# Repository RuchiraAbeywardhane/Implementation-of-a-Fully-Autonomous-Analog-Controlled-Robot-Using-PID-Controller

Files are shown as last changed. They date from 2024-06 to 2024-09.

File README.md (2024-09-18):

# Analog Wall Following Robot
This is a group project done under the module EN2091 - Laboratory Practice and Projects, Semester 3, Department of Electronic and Telecommunication Engineering, University of Moratuwa. 

## Introduction

*  Wall following robot is a robot that follows a wall and travels keeping a constant distance from the wall. 
*  Wall following is a common task in many robotics competitions.
*  But the interesting point is our project was to build a robot that travels on the centerline between two walls using only analog electronics.
*  That means we couldn’t use microcontrollers according to the [guidelines](https://github.com/LasithaAmarasinghe/Analog-Wall-Follow-Robot/blob/main/Project_Guidelines.pdf).

IMG-20231206-WA0097

## Working Concept

*  Two sharp IR sensors measure the distance from the robot to the side walls.
*  The difference between the sharp IR sensor values is taken as the error signal and fed into a PID control circuit.
*  The PID output signal is fed to the adder and subtractor circuits.
*  The PID output and a comparator circuit generate two PWM signals with varying duty cycles.
*  Then using the motor driver, PWM signals are fed to the left and right wheels.
*  The robot tracks the walls and travels on the centerline between walls.
*  Additionally we added another sharp IR sensor to the front of the robot to control the speed of the robot.
*  The measured distance is compared with a predefined distance and the difference is taken as the error signal.
*  The error signal is fed to a PID control circuit.
*  A PWM signal is generated using the PID output and a comparator circuit.
*  This PWM signal acts as the Base speed of the robot.
*  Consequently the additional sharp IR sensor will vary the car's speed accordingly.
*  Therefore the car will accelerate and deaccelerate according to the distance of the wall infront it.



## Sub Circuits and Tasks

* [Instrumentation Amplifier](https://github.com/LasithaAmarasinghe/Analog-Wall-Follow-Robot/blob/main/Circuits/Instrumentation%20Amplifier.jpg)- Reduce noise in Sharp IR sensor outputs and amplify signals
* [PID circuit](https://github.com/LasithaAmarasinghe/Analog-Wall-Follow-Robot/blob/main/Circuits/PID.jpg)- Control the error signal smoothly using feedback
* [Adder & Subtractor](https://github.com/LasithaAmarasinghe/Analog-Wall-Follow-Robot/blob/main/Circuits/Adder%20%26%20Substractor.jpg)- Generate two PWM signals with varying duty cycles according to PID output
	* Motor 1= base speed + PID output
	* Motor 2= base speed - PID output
* [PWM circuit](https://github.com/LasithaAmarasinghe/Analog-Wall-Follow-Robot/blob/main/Circuits/PWM.jpg)- Generate two different comparator voltages for the two motors
	* Motor 1 duty cycle ∝ base speed + PID output
	* Motor 2 duty cycle ∝ base speed - PID output
* [Voltage Regulator](https://github.com/LasithaAmarasinghe/Analog-Wall-Follow-Robot/blob/main/Circuits/Voltage%20Regulator.png)- To get 3.3V and 5V for required parts accordingly
* [Speed Selector](https://github.com/LasithaAmarasinghe/Analog-Wall-Follow-Robot/blob/main/Circuits/Speed%20Selector.png)- Manually control the base speed

## Hardware Specifications

* [TL084CN ICs](https://github.com/LasithaAmarasinghe/Analog-Wall-Follow-Robot/blob/main/data%20sheets/TL084CN_GeneralPurposeAmplifier.pdf)
* Two [Sharp IR Sensors](https://github.com/LasithaAmarasinghe/Analog-Wall-Follow-Robot/blob/main/data%20sheets/Sharp%20IR%20Sensor.pdf) 
* Two [N20 Motors](https://github.com/LasithaAmarasinghe/Analog-Wall-Follow-Robot/blob/main/data%20sheets/GA12-N20%20Motor.pdf)
* [L298N Motor Driver](https://github.com/LasithaAmarasinghe/Analog-Wall-Follow-Robot/blob/main/data%20sheets/L298%20Motor%20Driver.PDF)
* Wheels
* [Surface Mount Resistors](https://github.com/LasithaAmarasinghe/Analog-Wall-Follow-Robot/blob/main/Components/resistors.png)
* [Surface Mount Capacitors](https://github.com/LasithaAmarasinghe/Analog-Wall-Follow-Robot/blob/main/Components/capacitors.png)
* [Other Components](https://github.com/LasithaAmarasinghe/Analog-Wall-Follow-Robot/blob/main/Components/other%20components.png)

## Software Specifications

* Solid Works
* Altium Designer
* Multisim





## Enclosure Design

297237961-194de710-68c9-488a-863e-5720f45de2e3

## PCB Design

IMG-20231206-WA0012

## PCB



## Team Members

* Ruchira Abeywardhane
* Dinujaya Wijewickrama
* Lasitha Amarasinghe
* Sahan Abeyrathna

## License
 
 * This project is licensed under the MIT License. See the [LICENSE](MIT-LICENSE.txt) file for details.
   
## For More Information - [Project Report](https://github.com/LasithaAmarasinghe/Analog-Wall-Follow-Robot/blob/main/Project_Report.pdf)

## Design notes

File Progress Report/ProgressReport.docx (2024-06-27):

Done

1. A basic circuit for the circuit is implemented.
  a. Instrumentation Amplifier for taking data from the sensors.
  b. PID circuit
  c. Motor Controller
2. ICs are decided.
3. Have implemented the Proportional circuit, integrator and differentiator in simulation. (Simulation file is included in Simulations Folder)

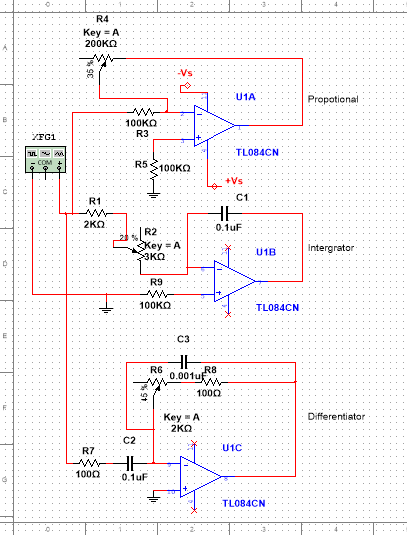
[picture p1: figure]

Needs to do

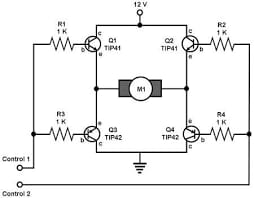
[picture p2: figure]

1. Have to simulate Motor Driver circuit. (When Control1=Varying Voltage and Control2=Varying Voltage M1 motor should rotate in one direction (speed have to change according to the varying voltage) and vise versa)
2. Must get familiarized (do a research) with how the PID tuning process works and what is the theory and concepts behind that.
3. And for the distance measurement the only option we have right now is SharpIR sensors. Drawback of the sharp IR sensor is minimum measurement it can do is 10cm, so the width of the road therefore will have to be minimum [20cm+the width of our robot] (And have to think about how are we going to position the sensors as well. The width of the road will change according to that). And that is not going to look very nice. So we have to find a distance measurement sensor which can measure at least a minimum distance of 5cm. The only requirement of the sensor is that it should output a voltage value which is proportional to the distance it is measuring. Or we have to come up with an alternative to reduce the width of the road while using SharpIR sensors.

Updated Speed Controller

If we take the x as the distance error to the front obstacle from the car. X is proportional to the speed. And therefore the oscilation is greater when x is large and fewer when x is small. Therefore we need to Take into account the error as well to determine the speed not only x. Error should be inversely propotional to the speed. Therefore eqn should be like this.

Speed = x + 1/E can not

Speed = x/E cannot

Speed = x – kE (cannot)

Speed = x – xE (0<E<k<1)

So the error needs to standardized to 0<E<1

So E function will be:

E>k : Then E=K

E<K: then E = E

So a Voltage Limiter is required. A 0.7V si Diode would be great.

A flusher for the intergrator. Manual neceassry. Auto have to think about it.

Check bandwidth of the opamp for 20KHZ PWM signal

Why 20Khz PWM?

And I mistakenly interchange the +Vs and -Vs of the power supply which burned 2 of the opamps. So we are gonna need to add something to prevent that to the SMD.

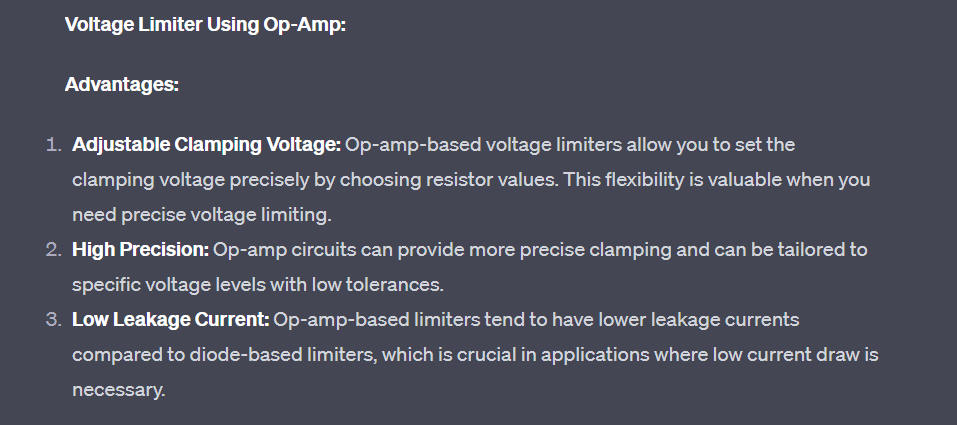
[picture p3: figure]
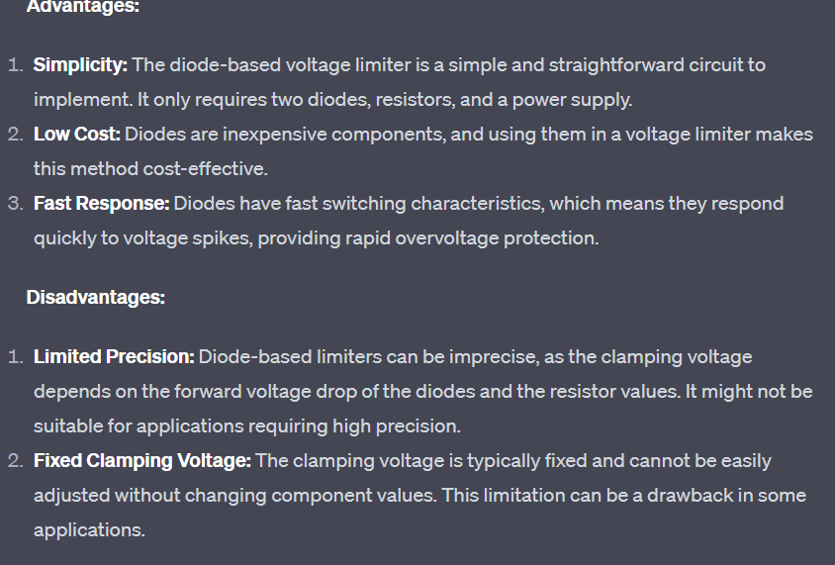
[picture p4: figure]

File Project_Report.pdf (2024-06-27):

Department of Electronic & Telecommunication Engineering, University of Moratuwa, Sri Lanka.

# Analog Wall Following Robot

Group Members:
210005H | Abeyrathna S.M.
210015M | Abeywardhane R.N.
210031H | Amarasinghe A.A.W.L.R.
210728C | Wijewickrama W.K.D.D.D.

Submitted in partial fulfillment of the requirements for the module EN 2091 Laboratory Practice and Projects

6th December 2023

Analog Wall Following Robot | Group No: 18 (Team Evoke)

## Contents

1 Introduction | 2
2 Component Selection | 2
3 System Architecture | 3
4 Functionality and Parameters | 4
5 PCB Design | 7
6 Enclosure Design | 7
7 Software Simulation and Hardware Testing | 8
8 Conclusion & Future Works | 9
9 Contribution of Group Members | 9

1

Abstract
The ability to follow walls is a common feature in many robots and micro-mouse vehicles, commonly designed using digital methods. However, our approach utilized analog methods exclusively. Every logical operation was executed through analog methods. Distances from the side and front walls were measured, and these measurements were processed through a PID algorithm-based circuit made with operational amplifiers and analog components. The resulting signals were then passed through adders and subtractors to generate appropriate signals for each wheel. Subsequently, the signals for motor control were generated by converting them with a PWM generator. Functionality was also added for selecting speed and tuning the PID. A PCB was designed to accommodate the circuit with Surface Mount Device (SMD) components, and a 3D-printed enclosure was designed and developed to support the structure created on the PCB appropriately.

## 1 Introduction

Wall following traditionally involves concatenating various logical elements through microcontroller programming. SharpIR sensors measure distances, and to refine the sensor outputs and eliminate noise, they are directed through instrumentation amplifiers. The logic for each wheel’s speed is then governed by two Proportional-Integral-Derivative (PID) circuits. One PID circuit, dedicated to side walls, determines wheel turning decisions, while the other, focused on the front, sets the base speed. The ”Adder Subtracter” circuit processes the PID outputs, generating distinct analog signals for each wheel. Since motor driver ICs do not accept analog signals, the obtained output signals are converted to Pulse Width Modulation (PWM) signals and fed to the motor driver IC. Additional functionalities include speed control, PID parameter tuning, and the ability to switch between linear travel mode and maneuvering bends.
Every functionality is meticulously implemented using analog circuits, divided into specific functional blocks:
1. Inputs and Instrumentational Amplifiers: Filtering signals from noisy inputs.
2. PID Wall: Following walls and executing turns.
3. PID Front: Decelerating during bends and controlling overall speed.
4. Adder and Subtractor: Generating separate signals for the left and right wheels.
5. PWM Generator: Creating PWM signals for the motor driver.
6. Speed Selector: Manually choosing the speed.

These functional blocks are uniquely crafted with operational amplifiers and other analog components.

## 2 Component Selection

### 2.1 SharpIR Sensor

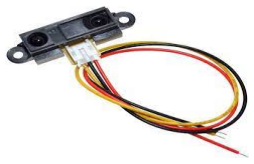
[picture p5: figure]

Figure 1: SharpIR Sensor

Instead of using an ultrasonic sensor, which is commonly used, we opted for the SharpIR sensor. This choice was made from the fact that the output of an ultrasonic sensor is calculated based on the delay between two pulses. In contrast, the SharpIR sensor provides a continuous analog signal proportional to the distance to the barrier. This feature was identified as ideal for analog purposes.

2

### 2.2 L298N Motor Driver

Figure 2:L298N Motor Driver IC

For efficient motor control and safety, we employ a motor driver to manage high currents. This component separates the logical analog circuit from the motor current, with motor control achieved through a PWM signal input.

### 2.3 TL084CN OP AMP

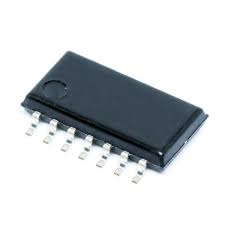
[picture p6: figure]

Figure 3: TL084CN OP AMP

To optimize PCB space, crucial for our design with over 50 op-amps, we strategically utilized the TL084CN, a Surface Mount Device (SMD)
IC containing four op-amps. | This choice sig-
nificantly reduced the required area. | Given
our application’s frequency requirements (below 200Hz), the slew rate became a less critical factor. Additionally, the TL084CN proved more power-efficient for our specific purpose compared to other op-amps available.

## 3 System Architecture

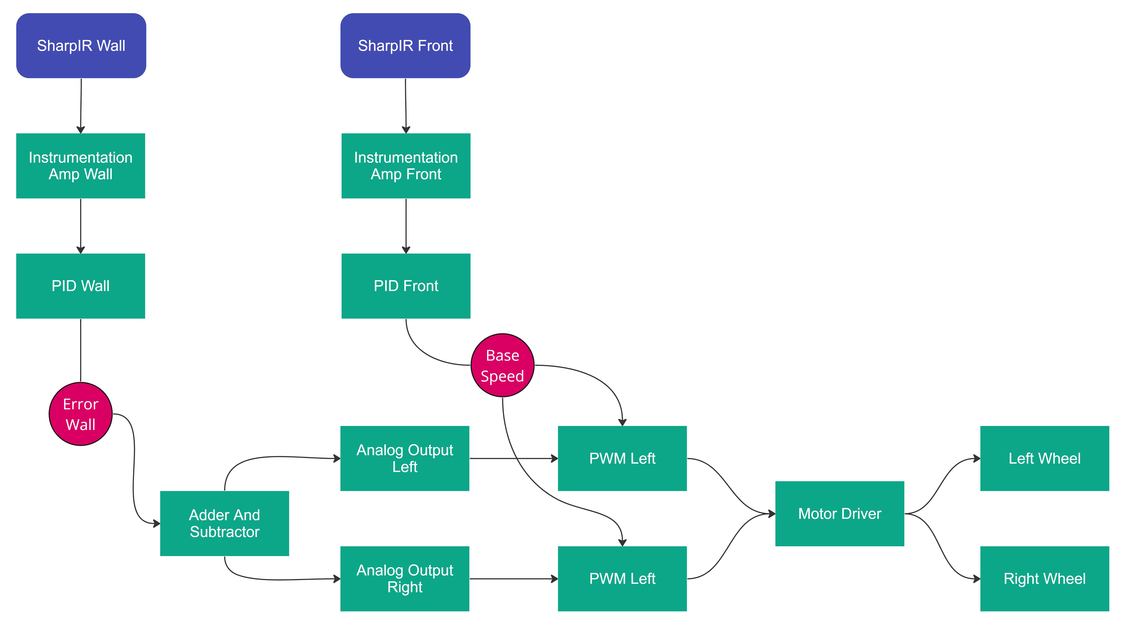
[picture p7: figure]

Figure 4: System Architecture

3

## 4 Functionality and Parameters

### 4.1 Instrumentation Amplifier

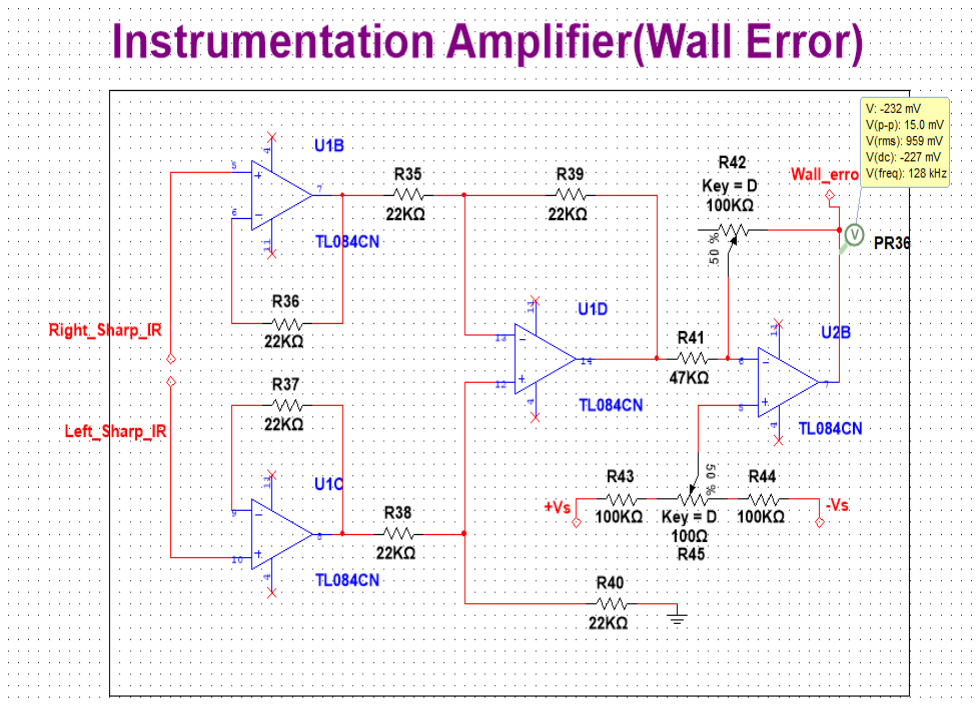
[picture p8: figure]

Figure 5: Instrumentation Amplifier

To address input signal noise in the PID circuit, we utilized an instrumentation amplifier. This component subtracts similar signals, minimizing the impact of disturbances. The input gain is adjustable with a potentiometer, ensuring precise control and effective noise reduction.

### 4.1.1 Output of the Instrumentation Am-

plifier

Output = Rvar
R41

(VIN1 − VIN2)

### 4.2 PID Wall Error

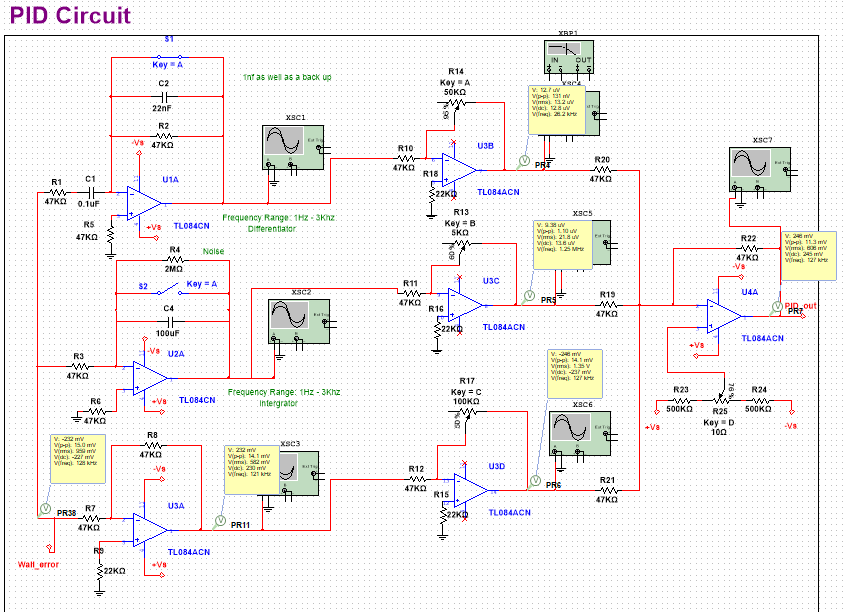
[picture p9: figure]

Figure 6: PID Wall Error

The wall error output from the instrumentation amplifier is directed to the PID circuit, determining the robot’s turning direction. The PID circuit independently computes differentiated, integrated, and proportional gains, combining them to determine the turning direction and angle effectively.

### 4.2.1 Propotionality of PID

Figure 6.1: PID Proportionality

It identifies the disparity between the distances to the left and right walls in real-time, generating an error signal. This error signal aids the robot in maintaining a centered position within the path. Output = Rvar
R

(W allError)

### 4.2.2 Differentiation of PID

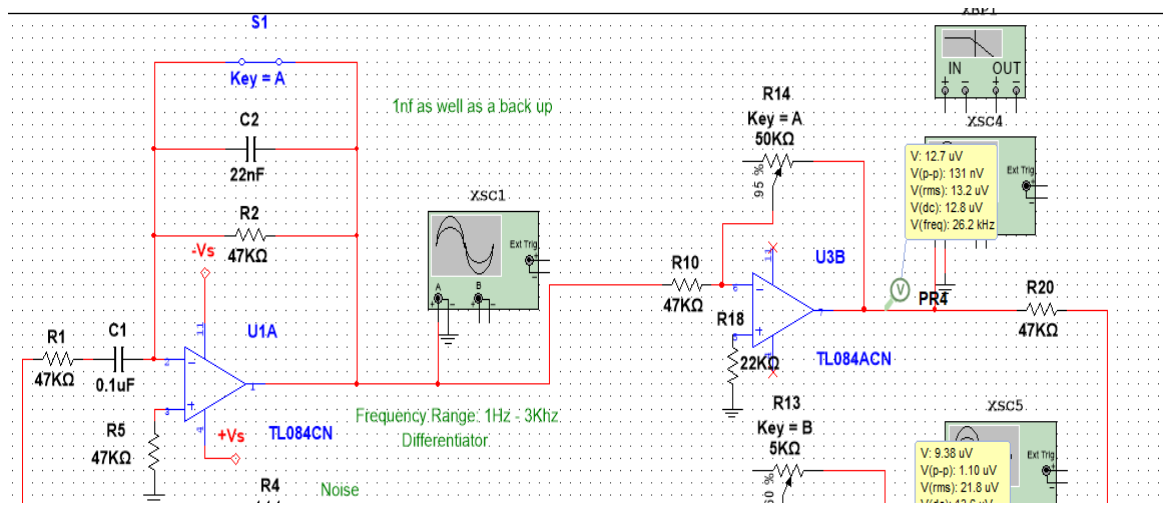
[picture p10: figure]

Figure 6.2: PID Differentiation

It identifies abrupt and gradual changes in the input, contributing to the robot’s smooth wall-following behavior. Additionally, it mitigates the oscillations introduced by the proportional section, ensuring more stable and controlled movement.
Output = Rvar
R
·

d
dt (Wall Error)

### 4.2.3 Integrator of PID

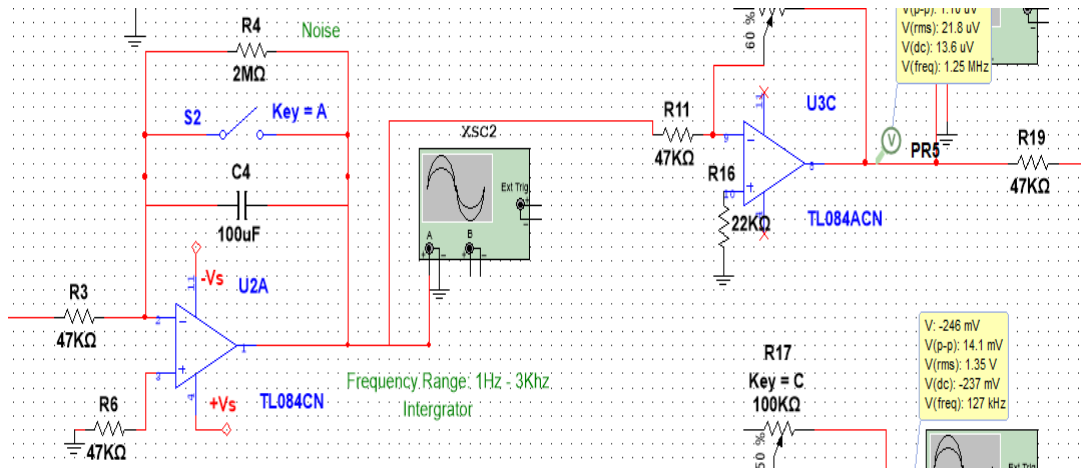
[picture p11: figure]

Figure 6.3: PID Integrator

4

While its direct impact on the final output is modest, this component plays a crucial role in improving the accuracy of wall following. It enhances stability, ensuring the robot maintains a correct center along the walls over time, preventing drift detected by the proportional section. Output = Rvar
R
·

R t
0 Wall Error dt

### 4.3 PID Distance Error

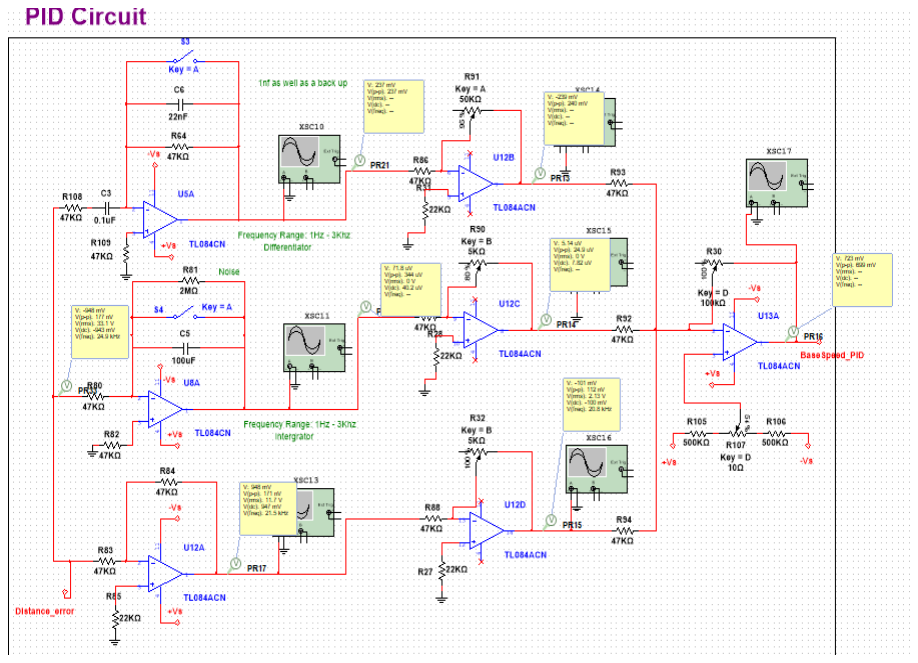
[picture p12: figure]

Figure 7: PID Distance Error

It evaluates the input from the front SharpIR sensor against a chosen base speed level. As the robot approaches a bend, the speed is proportionally reduced, facilitating precise and smooth turns. This process employs the familiar principles of proportionality, differentiation, and integration to compare with the established base speed.

### 4.4 Adder and Substractor

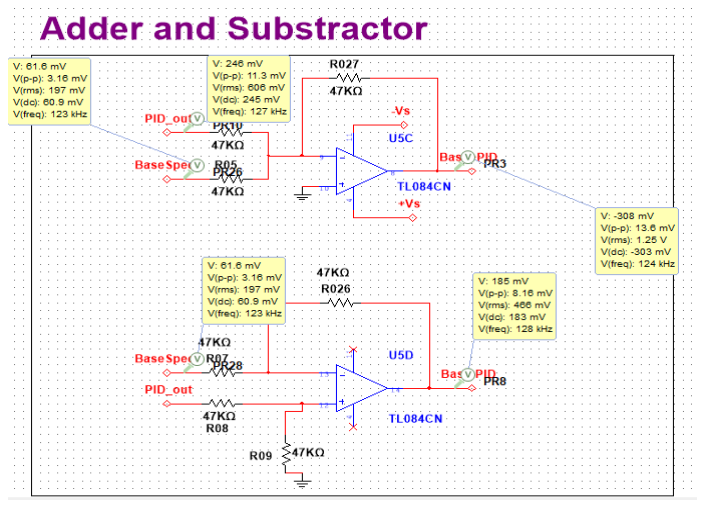
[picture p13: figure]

Figure 8: Adder and Substractor

It generates two distinct signals, namely Base + PID and Base - PID, providing separate outputs for the left and right wheels. This dual-signal approach contributes to differential control.

### 4.5 PWM Generator

Figure 9: PID Wall Error

TTo accommodate the digital input requirement of the motor driver, the analog modulated signal is converted to a Pulse Width Modulated (PWM) signal. This process involves a PWM generator that initially generates a triangular waveform. Subsequently, it compares the triangular wave with the provided signal, and the resulting compared output is clamped to produce a PWM signal.

### 4.5.1 PWM - Triangular Waveform Gen-

erator

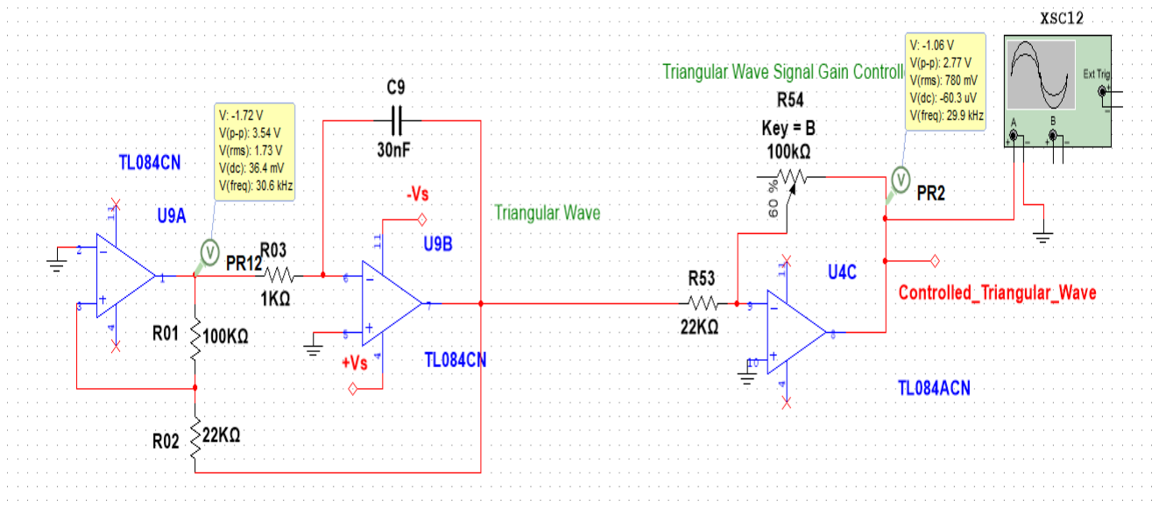
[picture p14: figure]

Figure 9.1: PWM Trangular

The triangular waveform generator is constructed by employing a ramp generator that undergoes inversion beyond a specific voltage threshold. The shape of the triangular waveform can be adjusted using a potentiometer, offering control over its characteristics.

5

### 4.5.2 PWM - Comparator

Figure 9.2: PWM Comparator

The generated triangular waveform is compared with the modulated analog signal, and the comparison results in cutoffs at various positions. The difference in positions where the cutoff occurs generates the Pulse Width Modulation (PWM) signal.

### 4.5.3 PWM - Clamper

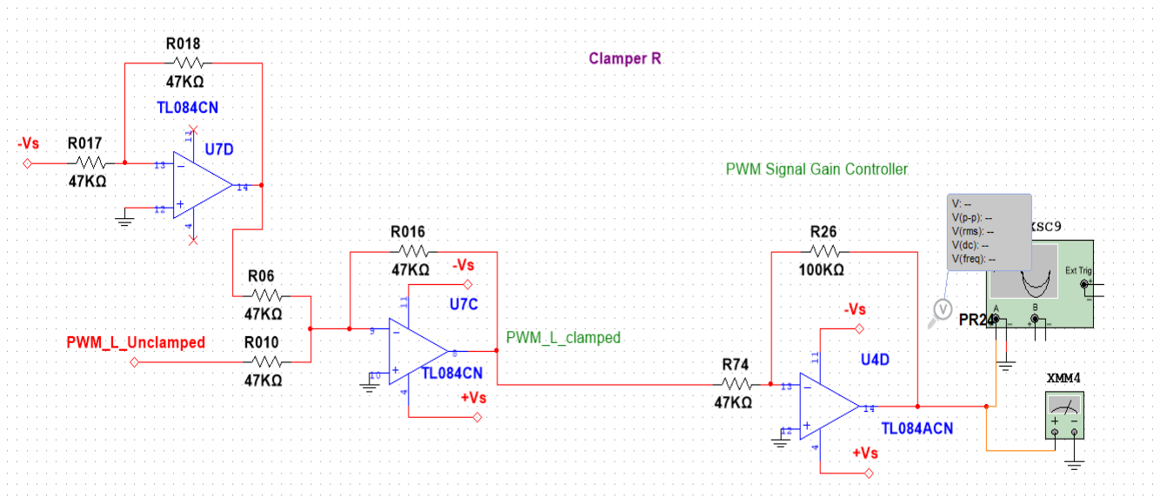
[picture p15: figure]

Figure 9.3: PWM Clamper

However, the output still consists of pulses with both positive and negative voltages. To obtain the desired Pulse Width Modulation (PWM) signal, the lowest voltage is set to 0, resulting in a signal that meets the required specifications.

### 4.6 Speed Selector

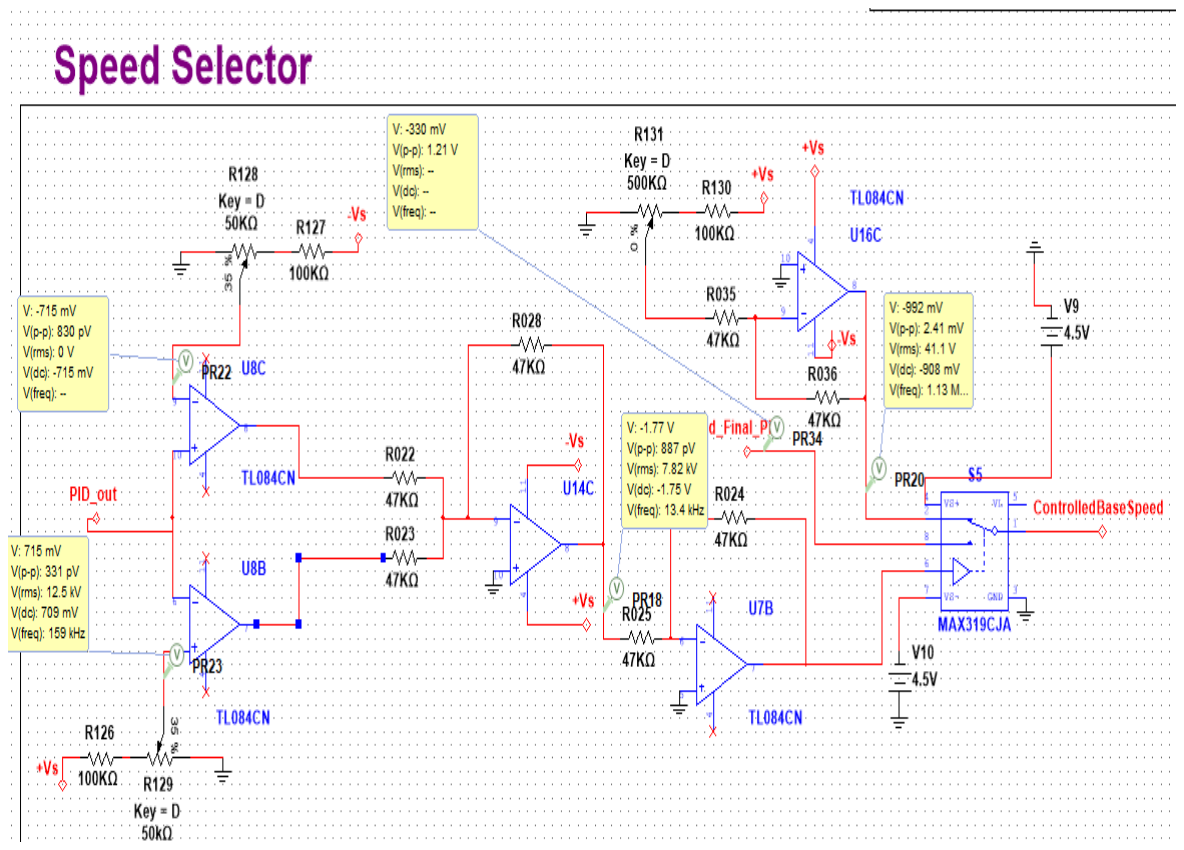
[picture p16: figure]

Figure 10: Speed Selector

This feature allows for the manual adjustment of the robot’s speed by altering the base speed setting.

### 4.7 Voltage Regulation

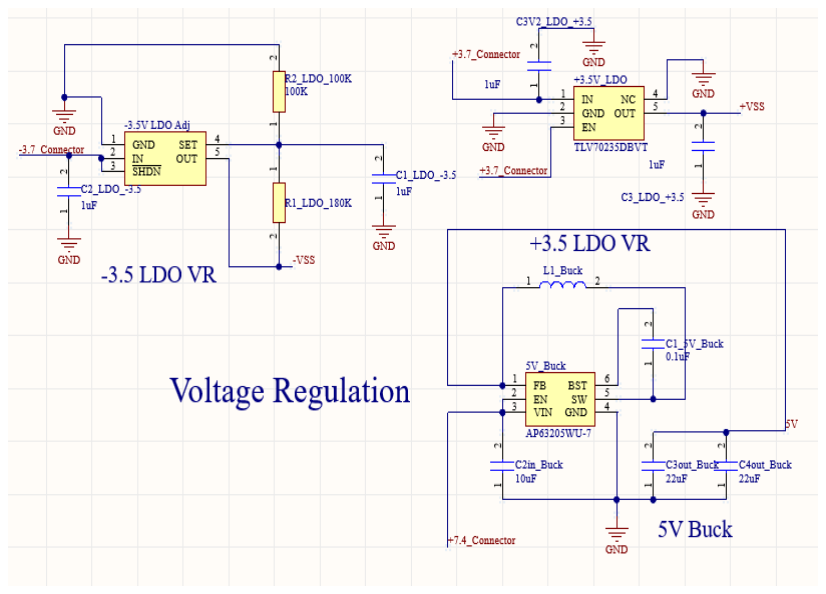
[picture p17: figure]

Figure 11: Power Supply Unit

This circuit segment takes power from the batteries and transforms it into 3.3V and 5V as needed for various sections of the robot.

6

## 5 PCB Design

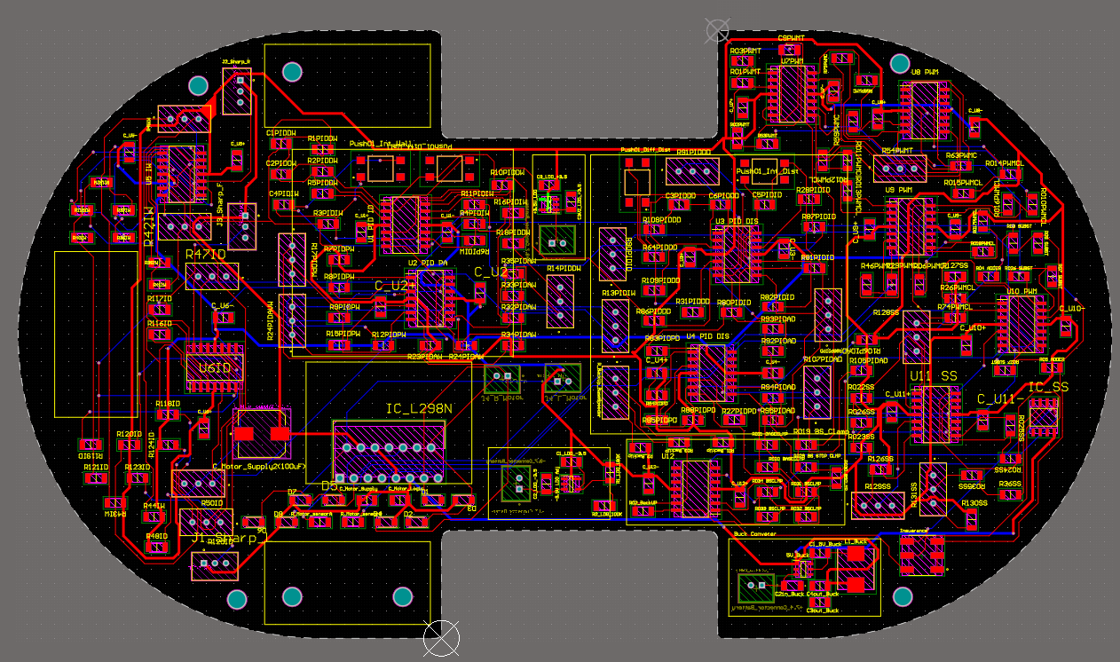
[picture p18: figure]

Figure 12.1:Top Layer | Figure 12.2:Bottom Layer

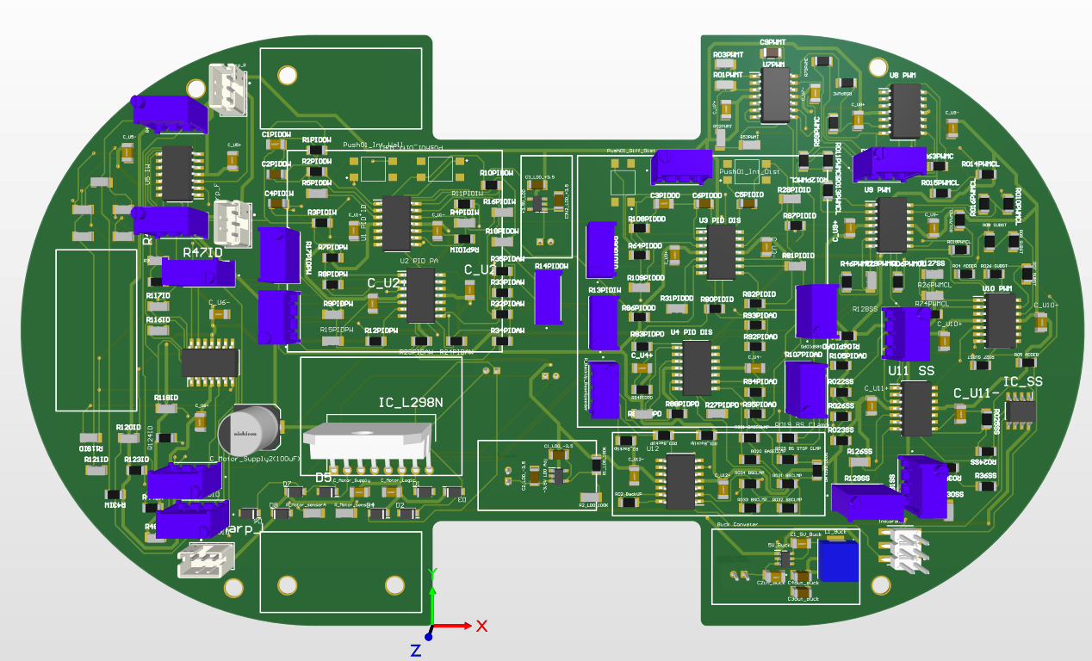
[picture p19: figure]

Figure 12.3: PCB 3d Top View

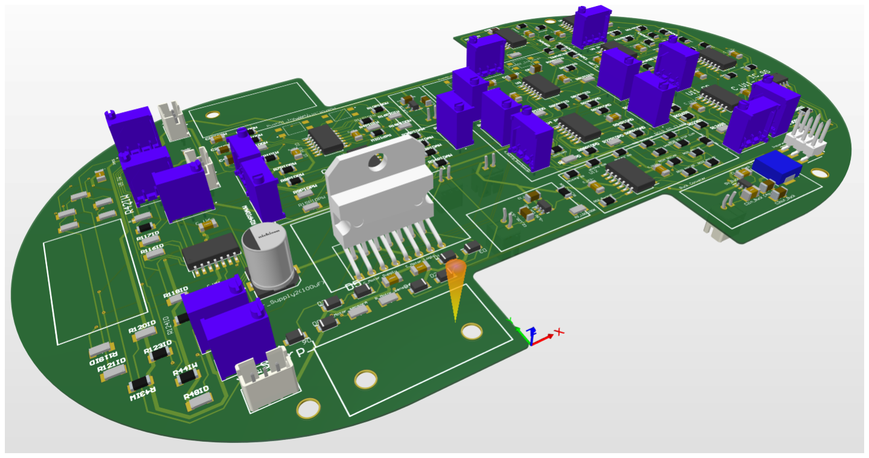
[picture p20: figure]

Figure 12.4: PCB 3d View

Utilizing Altium Designer, we meticulously crafted three printed circuit boards (PCBs) for the analog wall-following robot project: a power circuit, a wall-following circuit, and a motor control circuit. The PCB design employs multiple layers to optimize functionality. The top layer incorporates ground pour and +15V, seamlessly extending to the bottom layer for comprehensive routing. In the power supply PCB, a two-layer configuration is implemented, with one layer grounded to mitigate capacitance issues. Both lower layers feature integrated ground pours for heightened stability. To enhance versatility and ease of maintenance, IC bases are employed for all integrated circuits. The inclusion of pin headers and jumpers facilitates seamless connections between the ICs and external components, ensuring a modular and adaptable design.

## 6 Enclosure Design

Figure 13.1:Battery Holder1

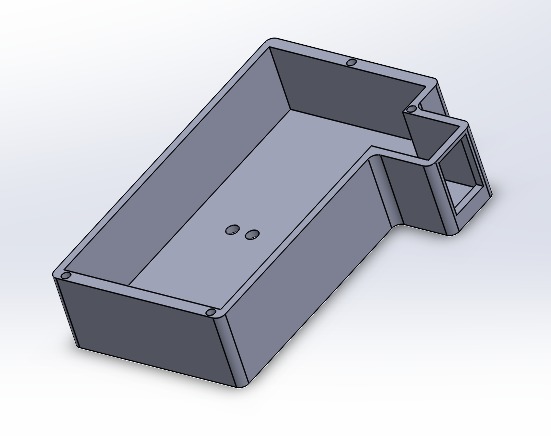
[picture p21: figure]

Figure 13.2:Battery Holder2

7

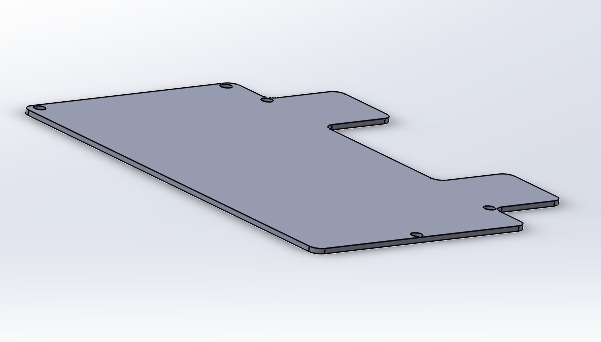
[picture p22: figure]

Figure 13.3: Battery Holder1 Cover

Figure 13.4: Battery Holder2 Cover

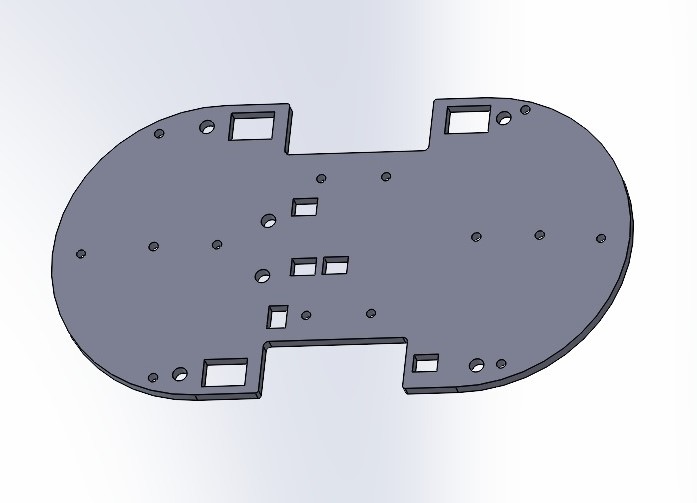
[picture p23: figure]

Figure 13.5: Chassis

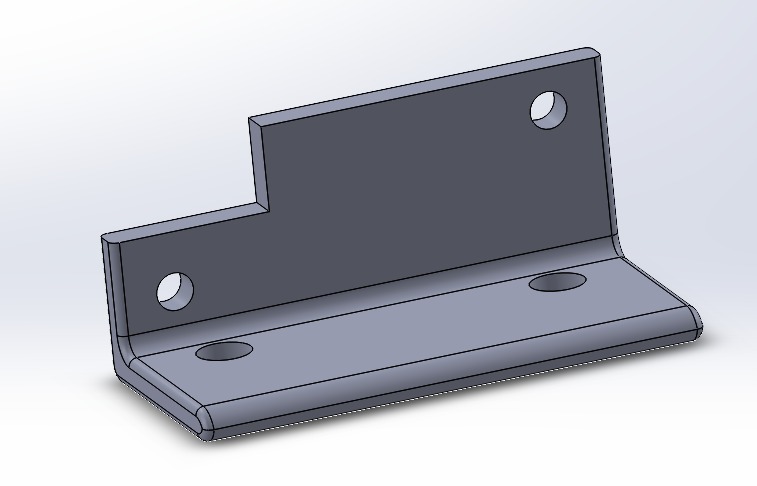
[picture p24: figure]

Figure 13.6: Sharp IR Sensor Holder

Using Solid Works, we designed enclosure designs for the analog wall-following robot project: three sharp IR sensor holders, two battery holders and the chassis.The chassis, modeled to adhere to the specified dimensions of 15 cm x 15 cm, serves as the structural backbone of the robot, providing a sturdy foundation for the electronic components. Precision in design was paramount, considering the 7 cm wall height and 30 cm width between walls, ensuring the robot can navigate through the designated space efficiently. The chassis is laser cut of plywood to make a simple design. The battery packs are 3D printed and attached at the bottom of the chassis. The sharp IR sensor holders are also 3D printed. Our enclosure design makes our robot a visually appealing robot.

## 7 Software Simulation and Hardware Testing


Figure 14.1:PWM Circuit Simulation

Figure 14.2:PWM Signals Simulation

8


Figure 14.3: PID Circuit Simulation | Figure 14.4: Adder Substractor Circuit Simulation

Figure 14.5: PWM signal testing


Figure 14.6: PID circuit testing

8 | Conclusion | & | Future
| Works

In conclusion, our analog wall-following robot project has successfully demonstrated the efficacy of analog methods in achieving precise and responsive navigation along walls. By eschewing conventional microcontroller-based programming in favor of analog circuitry, we have showcased a novel approach to wall-following that leverages operational amplifiers, PID algorithms, and analog components for logical operations. The integration of SharpIR sensors, instrumentation amplifiers, PID circuits, and the ”Adder Subtracter” circuit has yielded a robot capable of following walls with enhanced accuracy.
The conversion of analog signals into PWM signals for motor control further emphasizes the adaptability of analog methods in interfacing with motor driver ICs. The additional functionalities, including speed control, PID parameter tuning, and mode switching for linear travel and maneuvering bends, contribute to the versatility and user-friendliness of the robot.
Looking ahead, there are several avenues for future exploration and improvement. First and foremost, fine-tuning the PID parameters and optimizing the analog circuitry could enhance the robot’s responsiveness to different wall-following scenarios. Exploring alternative analog components and sensor configurations may offer opportunities for performance enhancements. Additionally, investigating power-efficient mechanisms and exploring energy harvesting methods could contribute to prolonged operational periods.
9 | Contribution | of | Group
| Members
Index Number | Contribution
210005H | Enclosure Designing
210015M | Circuit Designing & Simulation
210031H | Soldering & Testing
210728C | PCB Designing

9

## Acknowledgment

We would like to express our sincere gratitude to everyone who contributed to the successful completion of this analog wall-following robot project. Our heartfelt thanks go to our project supervisors Sasmitha Aiya, Vakeesan Aiya and Rajitha Aiya for providing valuable guidance, insights, and continuous support throughout the development process. Special appreciation is extended to each team member for their dedication, hard work, and collaborative spirit, which played a pivotal role in achieving the project objectives.

Furthermore, we appreciate the constructive feedback received during project reviews from Dr.Sampath Perera, Dr.Jayathu Samarawickrama, Dr.Chamira Edirisooriya & Dr.Samiru Gayan who significantly contributed to refining and improving the overall design. The encouragement and assistance from our peers and colleagues are also acknowledged with gratitude. This project has been a collective effort, and we are thankful for the collaborative environment that allowed us to explore, innovate, and overcome challenges. The invaluable experience gained from this project will undoubtedly shape our future endeavors.

## References

- PID-Theory
https://www.ni.com/en/shop/labview/pid-theory-explained.html
- DIY Circuit Design - Pulse Width Modulation (PWM) https://www.engineersgarage.com/diy-circuit-design-pulse-width-modulation-pwm/
- PID Controller
https://www.elprocus.com/the-working-of-a-pid-controller/
- The Working of Apractical-Integrator https://www.electronics-tutorial.net/analog-integrated-circuits/op-amp-integrator/practical-integrator/
- Ultrasonic-or-Infrared-Sensors
https://maxbotix.com/blogs/blog/ultrasonic-or-infrared-sensors/

10

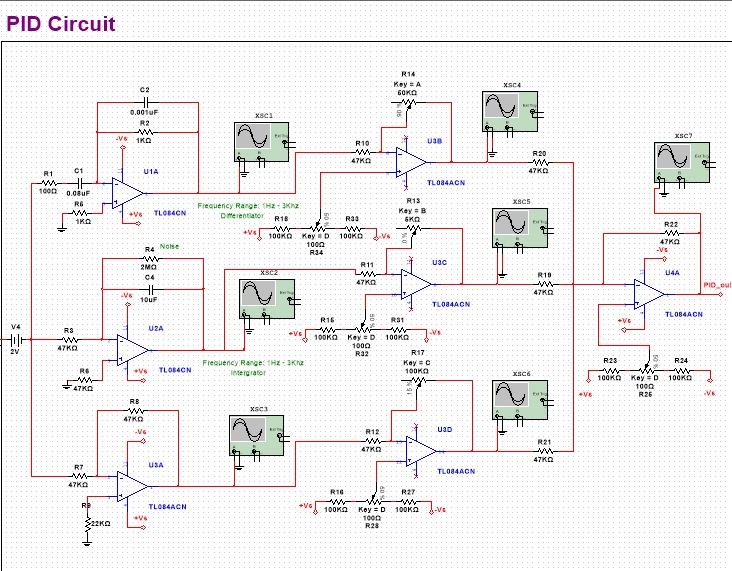
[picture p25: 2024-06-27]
Circuits/PID.jpg

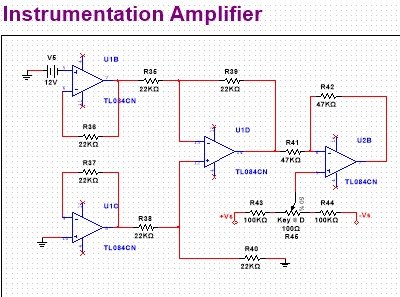
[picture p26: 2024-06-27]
Circuits/Instrumentation Amplifier.jpg

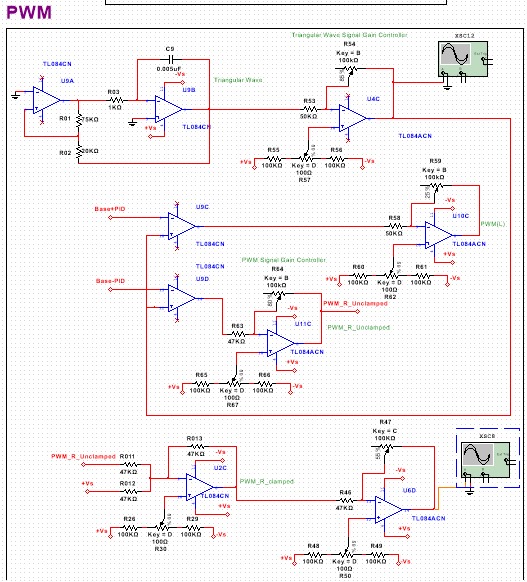
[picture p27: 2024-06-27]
Circuits/PWM.jpg

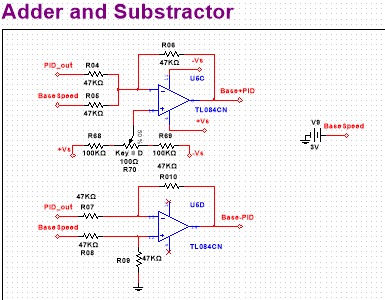
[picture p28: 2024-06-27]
Circuits/Adder & Substractor.jpg

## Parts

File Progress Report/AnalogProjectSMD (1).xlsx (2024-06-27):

Component | Footprint | Unit Price(10 or more) | Quantity | Total | Link | Datasheet
TL084CN | Available | 176.87 | 10 | 1768.7 | https://www.mouser.com/ProductDetail/Texas-Instruments/TL084CNSR?qs=AMJt07B76utXhWPN6gQoYQ%3D%3D | https://www.ti.com/lit/ds/symlink/tl081h.pdf?HQS=dis-mous-null-mousermode-dsf-pf-null-wwe&ts=1698124602865
Resistors 47Khoms | Available | 8.84 | 30 | 265.2 | https://www.mouser.com/ProductDetail/TE-Connectivity-Holsworthy/CRG1206F47K | https://www.mouser.com/datasheet/2/418/NG_CD_1623518_BA-686541.pdf
Resistors 22Khoms | Available | 9.5 | 30 | 285 | https://www.mouser.com/ProductDetail/Vishay-Dale/CRCW120622K0FKEAC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
Resistors 100Khoms | Available | 22 | 30 | 660 | https://www.mouser.com/ProductDetail/Vishay-Dale/CRCW1206100KFKTA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 | https://www.vishay.com/docs/20008/dcrcw.pdf
Resistor 1Kohms | Available | 12.77 | 10 | 127.7 | https://www.mouser.com/ProductDetail/Vishay-Draloric/RCA12061K00FKEA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 | https://www.mouser.com/ProductDetail/Vishay-Draloric/RCA12061K00FKEA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
Resistor 470ohms | Available | 47.17 | 10 | 471.7 | https://www.mouser.com/ProductDetail/Vishay-Dale/CRCW1206470RFKEAHP | https://www.vishay.com/docs/20043.pdf
Capacitors 100nF | Available | 26.86 | 10 | 268.6 | https://www.mouser.com/ProductDetail/KEMET/C1206C104K5RAC7867 | https://www.mouser.com/datasheet/2/447/KEM_C1002_X7R_SMD-3316098.pdf
Buck Converter 6V | Available | 735 | 1 | 735 | https://www.mouser.com/ProductDetail/Infineon-Technologies/IR3823AMTRPBFAUMA1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 | https://www.mouser.com/datasheet/2/196/Infineon_IR3823AMTRPBF_DataSheet_v02_40_EN-3165844.pdf
Buck Converter 3.3V | Available | 660 | 1 | 660 | https://www.mouser.com/ProductDetail/Nisshinbo/RP402N301F-TR-FE?qs=1cUJgmOA5AeJXrp3zn8QMw%3D%3D | https://www.mouser.com/datasheet/2/294/rp402_ea-3219487.pdf
6V N20 200RPM motors |  | 1190 | 2 | 2380 | https://scionelectronics.com/product/ga12-n20-10mm-long-axis-mini-gear-motor-6v-200rpm/
D hole Rubber wheels for N20 |  | 200 | 2 | 400 | https://tronic.lk/product/d-hole-rubber-wheel-for-n20-motor-32x7mm-hole-3mm
Total |  |  |  | 7621.9

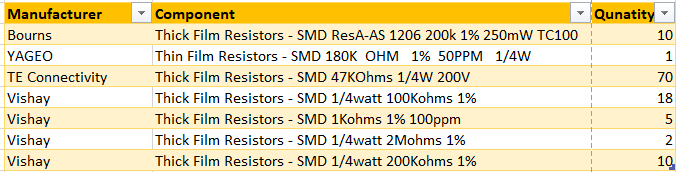
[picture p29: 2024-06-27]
Components/resistors.png

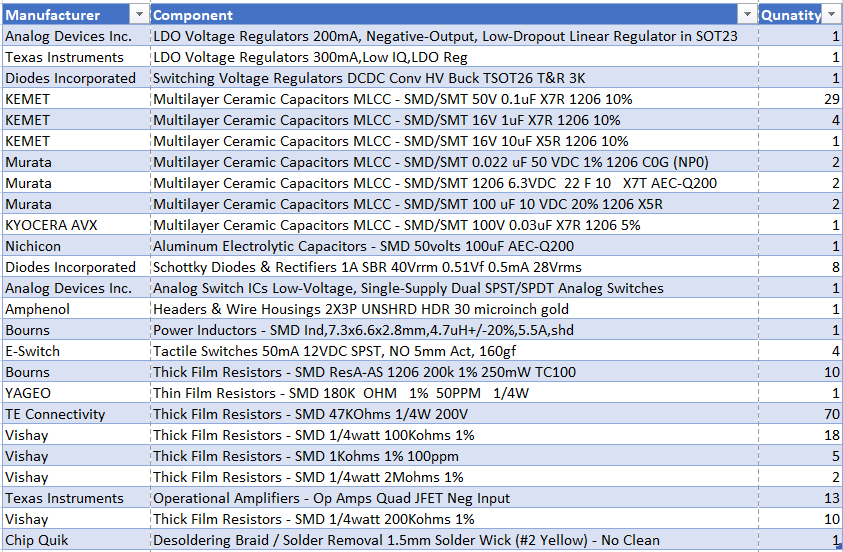
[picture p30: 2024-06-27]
Components/all components.png

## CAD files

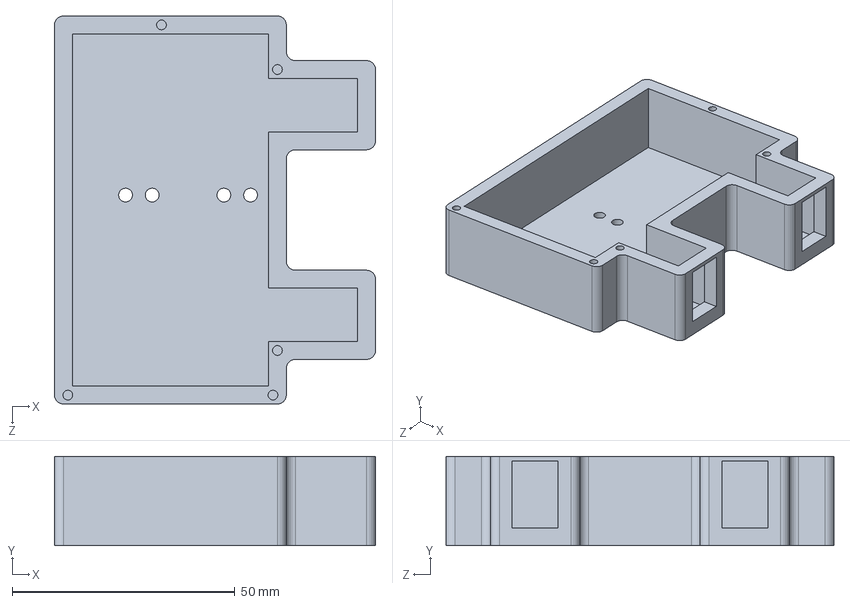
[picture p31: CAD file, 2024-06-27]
Solidwork files/analog battery pack front.SLDPRT
72.0 x 20.0 x 87.0 mm

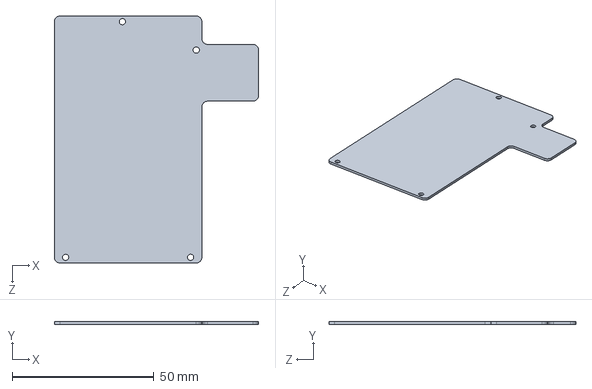
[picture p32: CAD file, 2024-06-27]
Solidwork files/battery lid rear.SLDPRT
72.0 x 1.00 x 87.0 mm

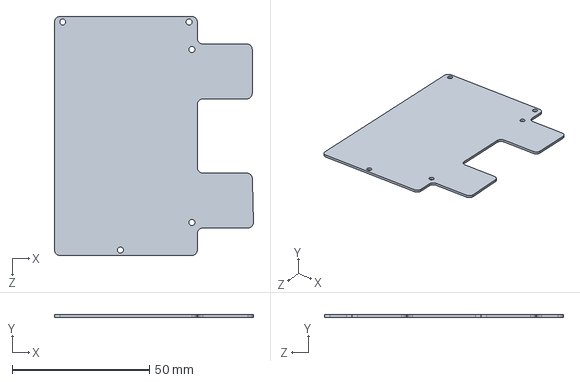
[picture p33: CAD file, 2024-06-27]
Solidwork files/battery lid front.SLDPRT
72.4 x 1.00 x 87.0 mm

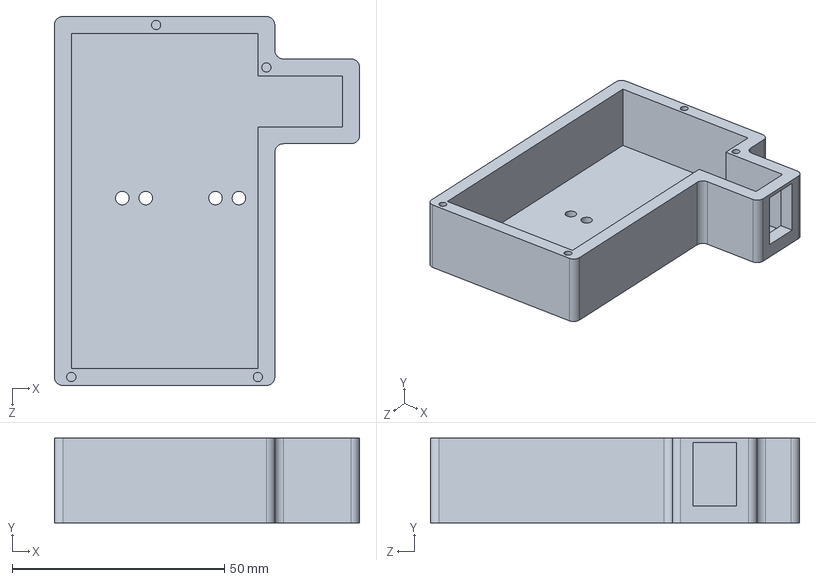
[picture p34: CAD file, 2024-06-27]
Solidwork files/analog battery pack 2.SLDPRT
72.0 x 20.0 x 87.0 mm
